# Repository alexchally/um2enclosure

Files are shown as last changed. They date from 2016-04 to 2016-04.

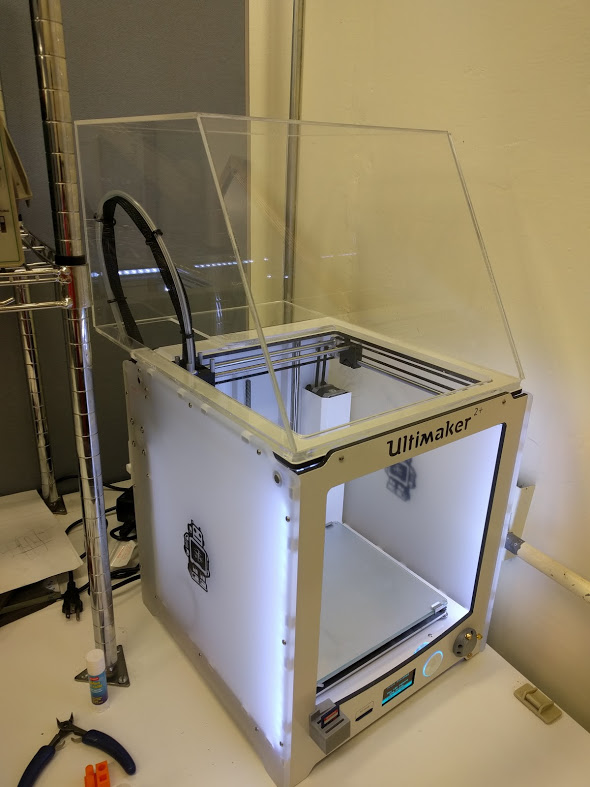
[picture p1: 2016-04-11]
ultimaker 2 enclosure example.jpg

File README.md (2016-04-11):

# um2enclosure
A laser cut enclosure for the Ultimaker 2

Credit where credit is due: While I drew this up by myself, it is basically a quick redesign of the enclosure made by Bertho Boman here: https://www.youmagine.com/designs/bertho-boman--2

This enclosure is meant to be cut out of 5/16" acrylic with a true thickness of .171". It was designed to fit an Ultimaker 2+. 

All files were designed in Freedom Units (IPS)

BOM: 
Acrylic or wood panels, roughly .171" thick. I would include an exact BOM, but everyone's laser cutter is a bit different, so arrange the design for yourself before you go buy stock so you can minimize waste. 

Glue for your material of choice

Instructions: 

Cut one of each file except sides, which you should cut 2. 

Use acrylic glue to glue them all together. THE ENCLOSURE BASE AND ENCLOSURE BOX BOTTOM MUST BE GLUED TOGETHER IN A PARTICULAR ORIENTATION, WITH THE CUTOUTS FOR THE BOWDEN TUBE MATCHED. Use the exploded diagram or the solidworks assembly as a guide. Glue up on a big box like this can be tricky, so make sure you use lots of clamps and check the squarenss of everything before it goes togehter. I suggest starting with the base, then the back and sides, then the top, then the front. Pay attention to which panel is on the "outside" when putting edges up against each other. 

Please be careful, acrylic is flamable and a malfunctioning 3d printer has the potential to burn your house down, so use at your own risk.

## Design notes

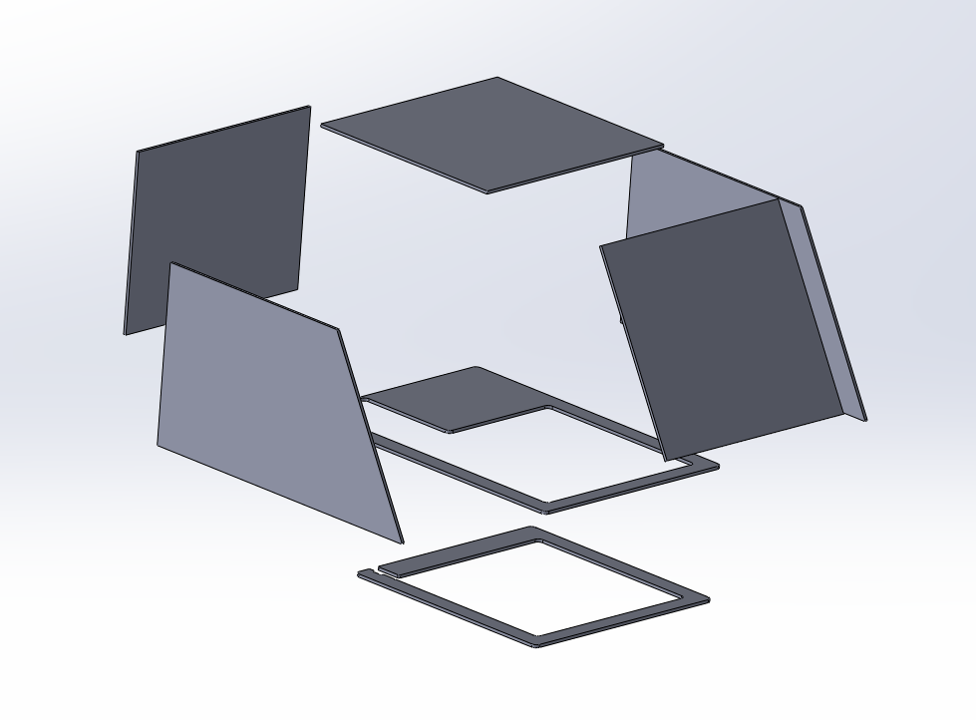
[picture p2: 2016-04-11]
explodedview.png

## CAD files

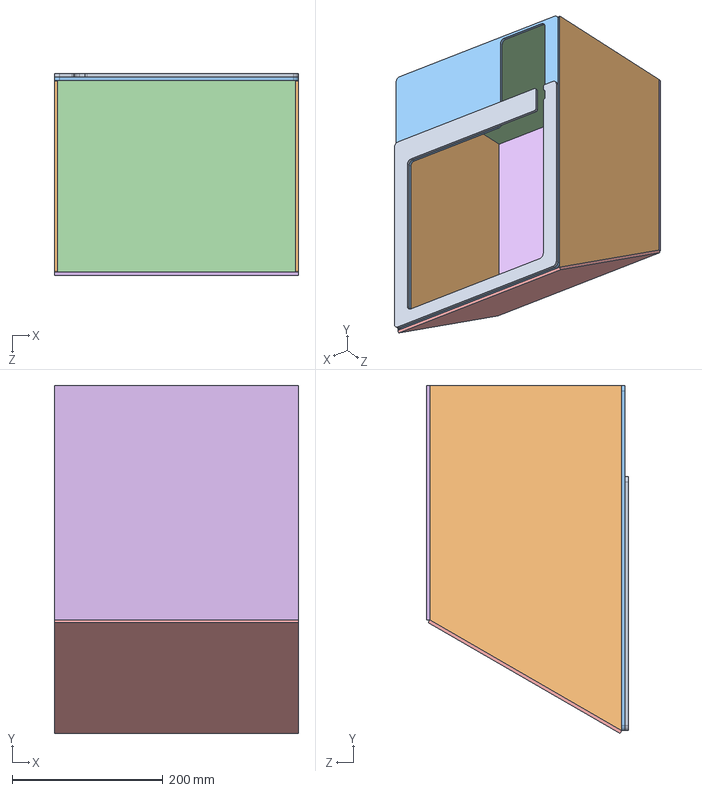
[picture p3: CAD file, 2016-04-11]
solidworks files/Enclosure Assembly.SLDASM
323.9 x 461.0 x 267.0 mm
enclosure base
Sides x 2
enclosure box bottom
back
front
top

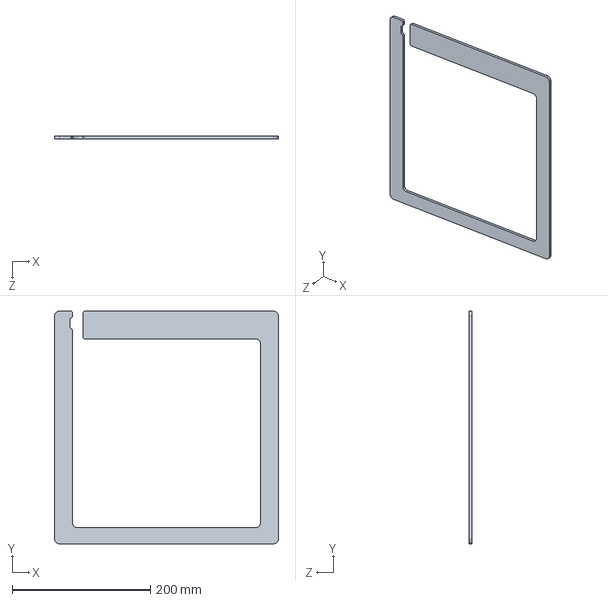
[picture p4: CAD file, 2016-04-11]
solidworks files/enclosure base.SLDPRT
323.9 x 336.5 x 4.34 mm

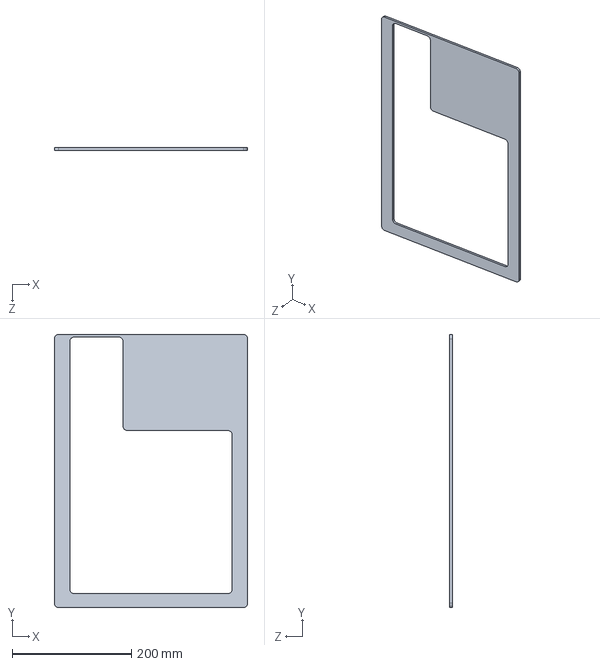
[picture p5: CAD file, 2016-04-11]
solidworks files/enclosure box bottom.SLDPRT
323.9 x 457.2 x 4.34 mm

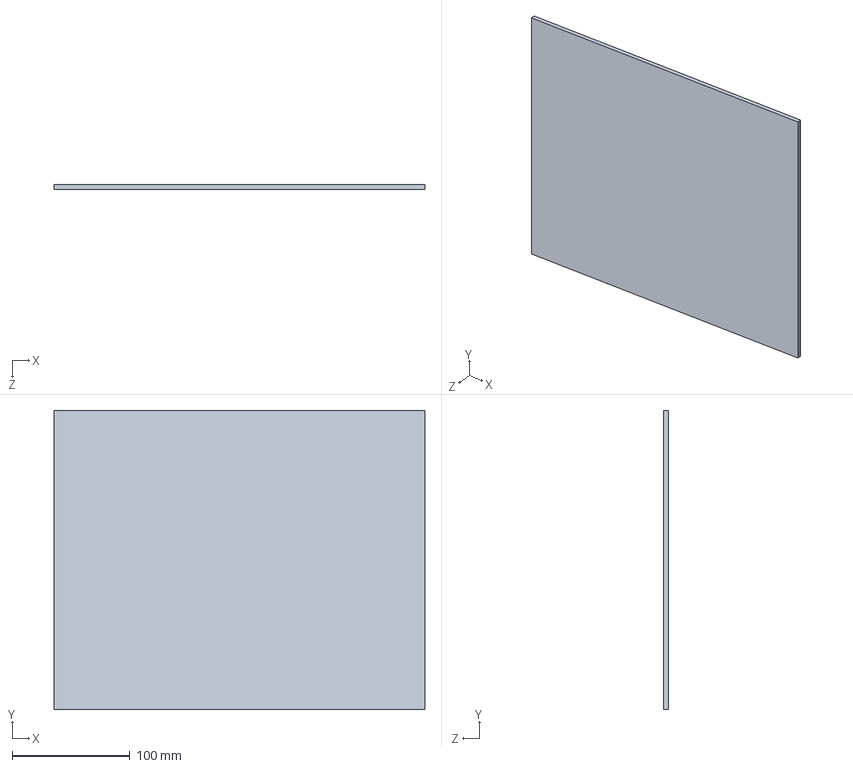
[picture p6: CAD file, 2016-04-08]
solidworks files/back.SLDPRT
315.2 x 254.0 x 4.34 mm

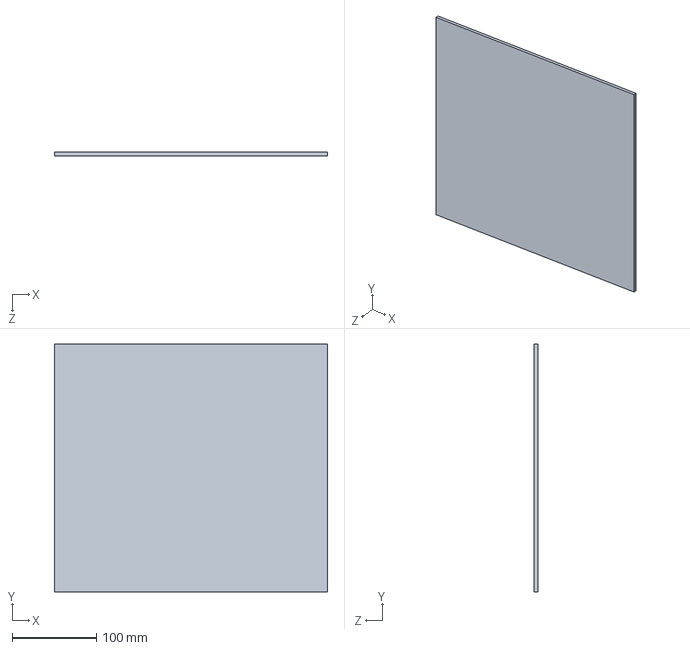
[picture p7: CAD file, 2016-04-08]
solidworks files/front.SLDPRT
323.9 x 293.7 x 4.34 mm

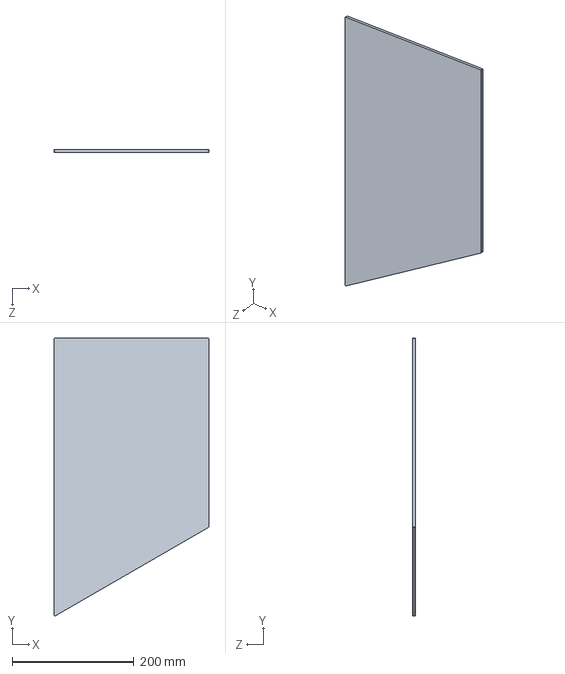
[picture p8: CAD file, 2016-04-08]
solidworks files/Sides.SLDPRT
254.0 x 456.3 x 4.34 mm

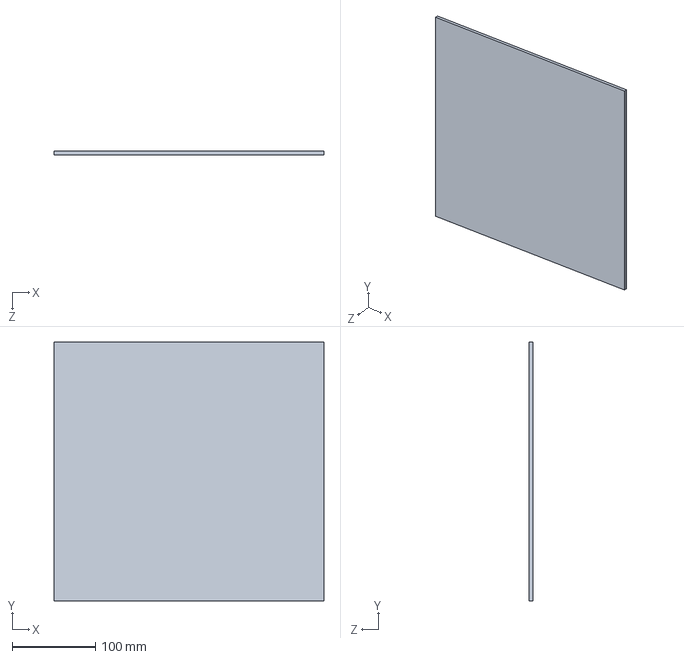
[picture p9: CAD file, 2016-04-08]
solidworks files/top.SLDPRT
323.9 x 310.3 x 4.34 mm

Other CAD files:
Enclosure Assembly.STL
dxf files/Sides.DXF
dxf files/back.DXF
dxf files/enclosure base.DXF
dxf files/enclosure box bottom.DXF
dxf files/front.DXF
dxf files/top.DXF

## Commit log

2016-04-08 Initial Upload
    [Enclosure Assembly.SLDASM, Enclosure Assembly.STEP, Sides.DXF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]
2016-04-08 added stl file and deleted step file.,
    [Enclosure Assembly.STEP, Enclosure Assembly.STL]
2016-04-08 updated position of through hole
    [Enclosure Assembly.STL, enclosure base.DXF, enclosure box bottom.DXF]
2016-04-11 Update after first assembly
    I updated everything after assembling the first enclosure so that it
    reflected the as built design. I included more assembly instructions in
    the readme, a picture of a completed enclosure, and an exploded diagram.
    [Enclosure Assembly.SLDASM, enclosure base.SLDPRT, enclosure box bottom.SLDPRT]
